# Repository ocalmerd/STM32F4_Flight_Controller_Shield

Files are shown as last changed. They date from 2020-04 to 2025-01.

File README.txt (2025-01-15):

Software is prepared as an Embedded C software, targetted to the STM32F407VGT6U MCU.
Hardware part is designed in Altium Designer and schematics & PCB design in ".Hardware" folder.

MERT OCAL

ocalmerd@gmail.com / mert.ocal@ogr.sakarya.edu.tr

https://www.linkedin.com/in/mert-ocal71/ / https://github.com/ocalmerd/

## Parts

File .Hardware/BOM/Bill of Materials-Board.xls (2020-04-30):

Item # | Designator | Description | Name | Quantity | Manufacturer 1 | Manufacturer Part Number 1 | Footprint | LibRef | Note
1 | C1, C2 | 220µF 16V Aluminum Electrolytic Capacitors Radial, Can - SMD 1000 Hrs @ 105°C | CAP ALUM 220UF 20% 16V SMD | 2 |  |  | CAP ALUM 6.6MM | 100uF 16V Aluminum(POL)
2 | D1 | Schottky Rectifier | SMAJ5.0A TVS Diyot | 1 |  |  | DO214AC SMA | SMAJ5.0A
3 | J1 | DC Power Jack Connector WR-DC, Male, Right Angled, THT, 5 A, 24 V | DC Power Jack | 1 |  |  | 694106301002 | 694106301002
4 | J2 | Header, 25-Pin, Dual row | Left Pins Connector | 1 |  |  | HDR2X25 | Header 25X2
5 | J3 | Header, 25-Pin, Dual row | Right Pins Connector | 1 |  |  | HDR2X25 | Header 25X2
6 | J4 | Header, 9-Pin | L3GD20H Connector | 1 |  |  | HDR1X9 | Header 9
7 | J5 | Header, 6-Pin, Right Angle | R9DS Receiver Connector | 1 |  |  | HDR1X6H | Header 6H
8 | J6 | Header, 4-Pin, Right Angle | 433MHz Air Connector | 1 |  |  | HDR1X4H | Header 4H
9 | J7 | Header, 3-Pin, Right Angle | ESC1 Connector | 1 |  |  | HDR1X3H | Header 3H
10 | J8 | Header, 3-Pin, Right Angle | ESC2 Connector | 1 |  |  | HDR1X3H | Header 3H
11 | J9 | Header, 3-Pin, Right Angle | ESC3 Connector | 1 |  |  | HDR1X3H | Header 3H
12 | J10 | Header, 3-Pin, Right Angle | ESC4 Connector | 1 |  |  | HDR1X3H | Header 3H
13 | U1 | Buck Switching Regulator IC Positive Fixed 5V 1 Output 3A TO-263-6, D²Pak (5 Leads + Tab), TO-263BA | LM2576HVS-5.0 REG BUCK 5V 3A TO263-5 | 1 |  |  | TO-263-6 | LM2576HVS-5.0--

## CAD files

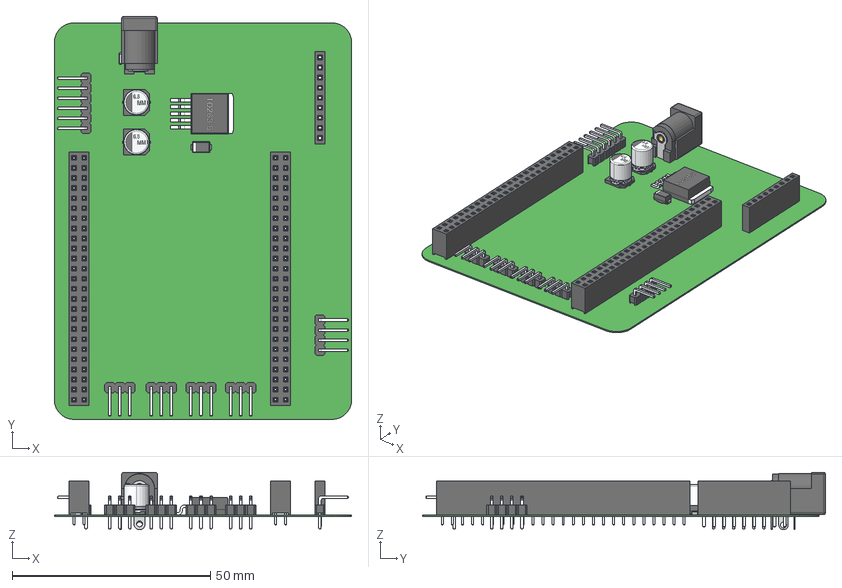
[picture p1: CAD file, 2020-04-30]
.Hardware/ExportSTEP/Board.step
75.0 x 101.6 x 14.5 mm
CAP_ALUM_6_6mm x 2
to263-5_p1-7_l10-2_w9-45
6941xx301002
694106301002_PinContact
6941xx301002_Back
6941xx301002_PinContact2
6941xx301002_PinLame
6941xx301002_PinBis
SMA

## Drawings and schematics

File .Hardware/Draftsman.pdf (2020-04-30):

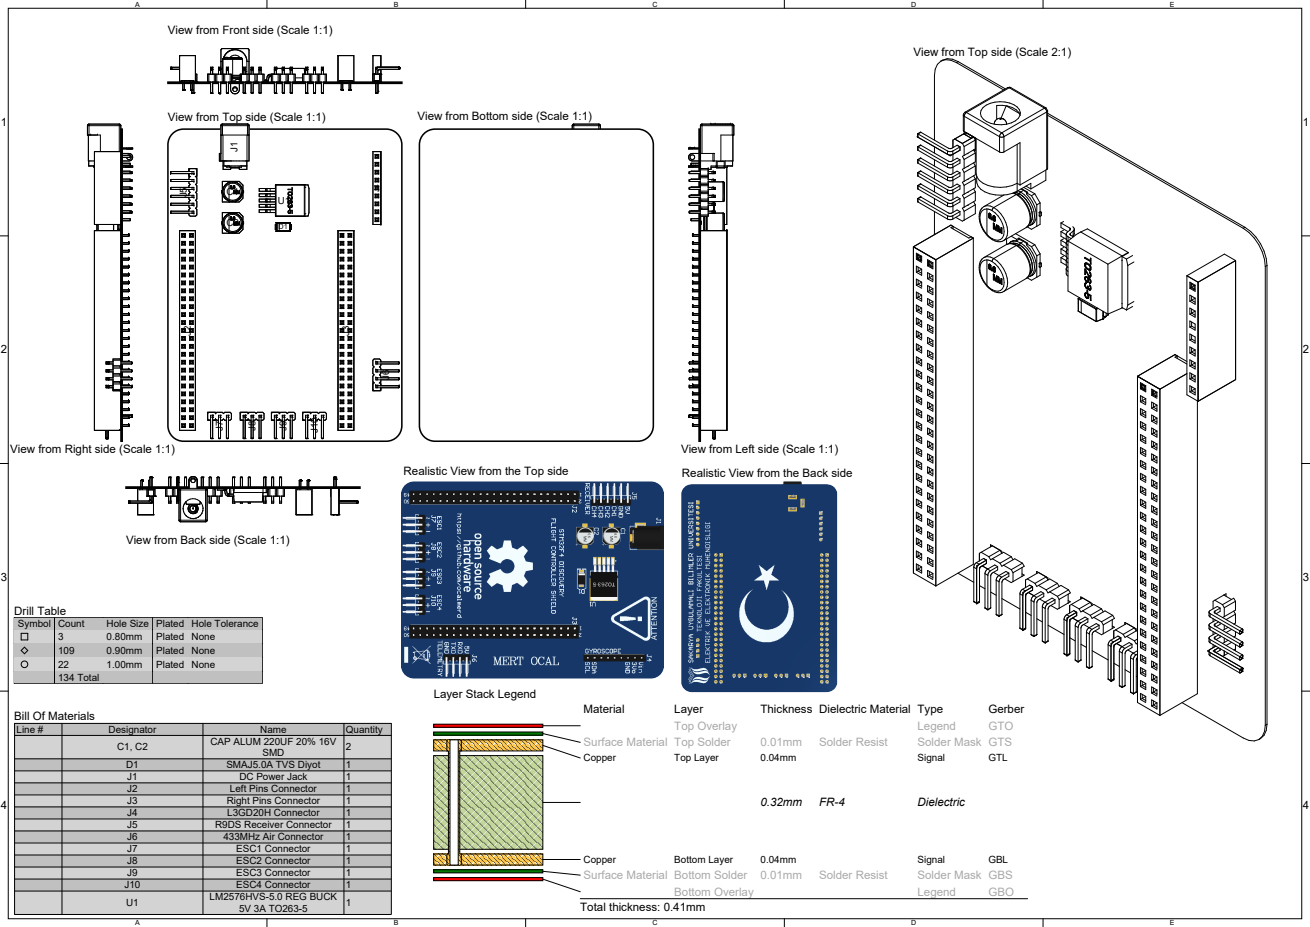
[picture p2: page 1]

View from Front side (Scale 1:1)

View from Top side (Scale 2:1)

View from Back side (Scale 1:1)

Symbol | Count | Hole Size | Plated | Hole Tolerance

3 | 0.80mm | Plated | None
109 | 0.90mm | Plated | None
22 | 1.00mm | Plated | None
134 Total

Line # | Designator | Name | Quantity

C1, C2 | CAP ALUM 220UF 20% 16V SMD | 2

D1 | SMAJ5.0A TVS Diyot | 1
J1 | DC Power Jack | 1
J2 | Left Pins Connector | 1
J3 | Right Pins Connector | 1
J4 | L3GD20H Connector | 1
J5 | R9DS Receiver Connector | 1
J6 | 433MHz Air Connector | 1
J7 | ESC1 Connector | 1
J8 | ESC2 Connector | 1
J9 | ESC3 Connector | 1
J10 | ESC4 Connector | 1
U1 | LM2576HVS-5.0 REG BUCK 5V 3A TO263-5 | 1

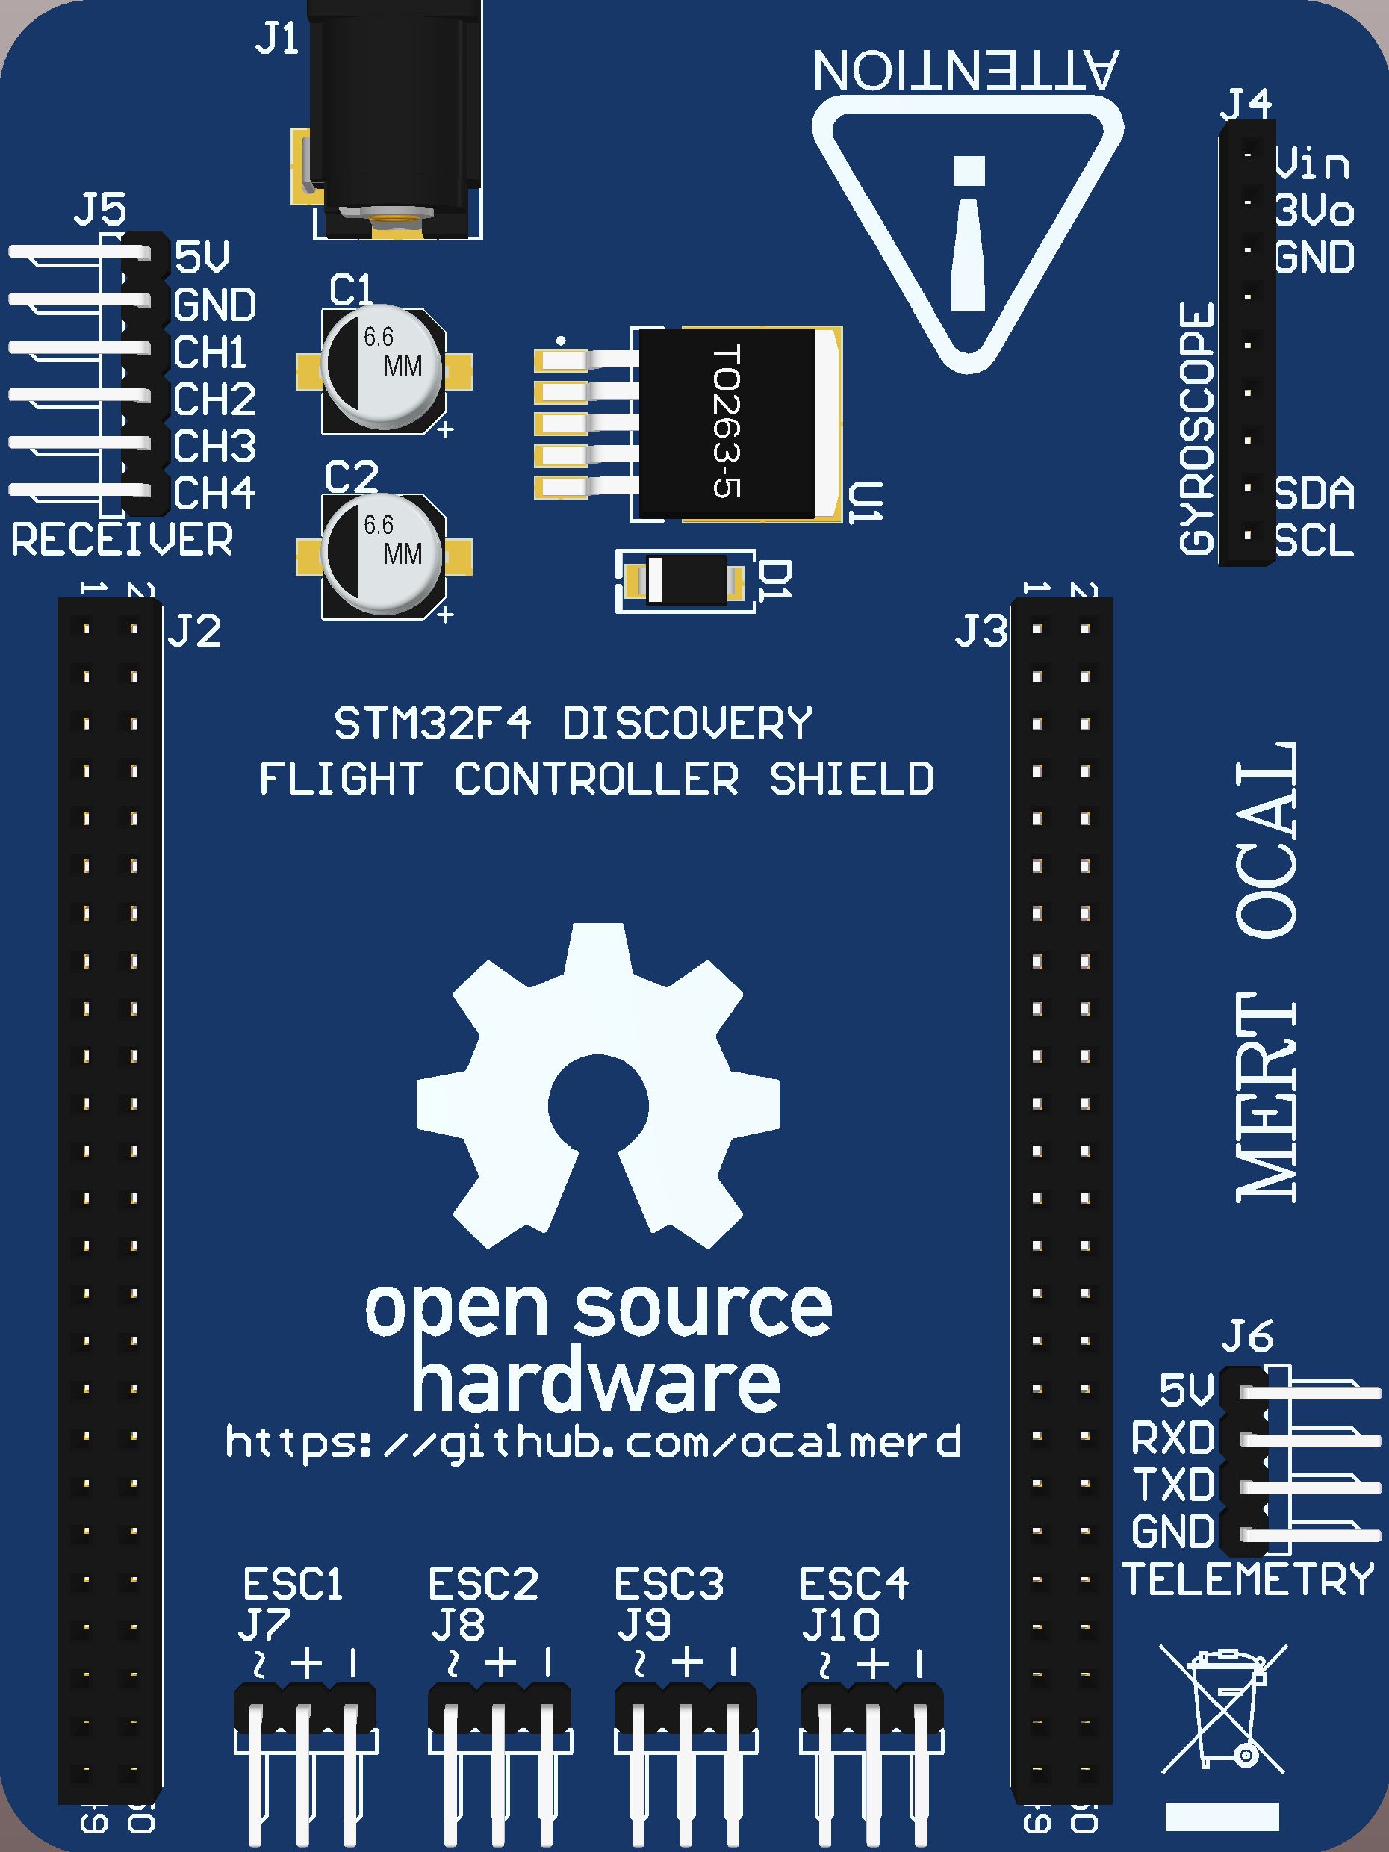
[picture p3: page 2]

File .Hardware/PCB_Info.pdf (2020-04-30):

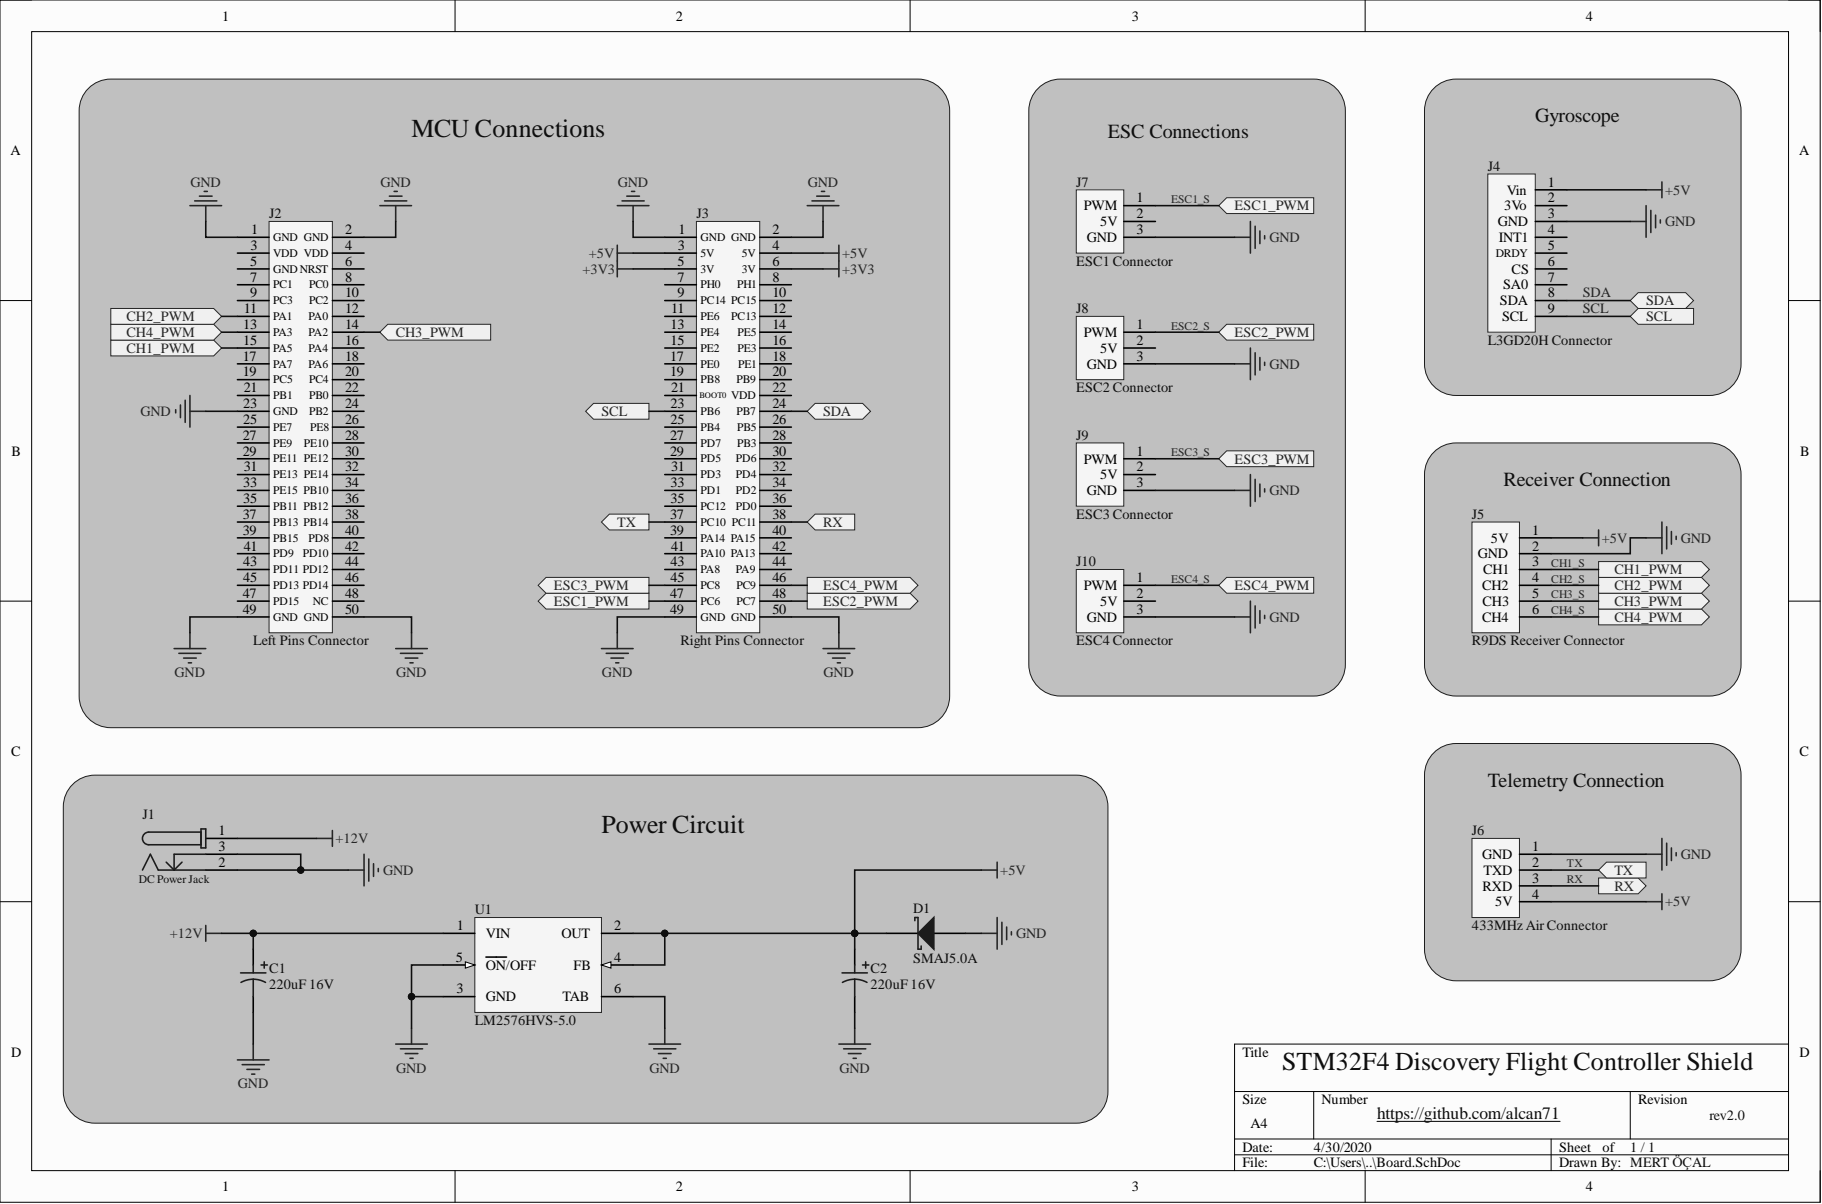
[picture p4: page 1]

Title
STM32F4 Discovery Flight Controller Shield

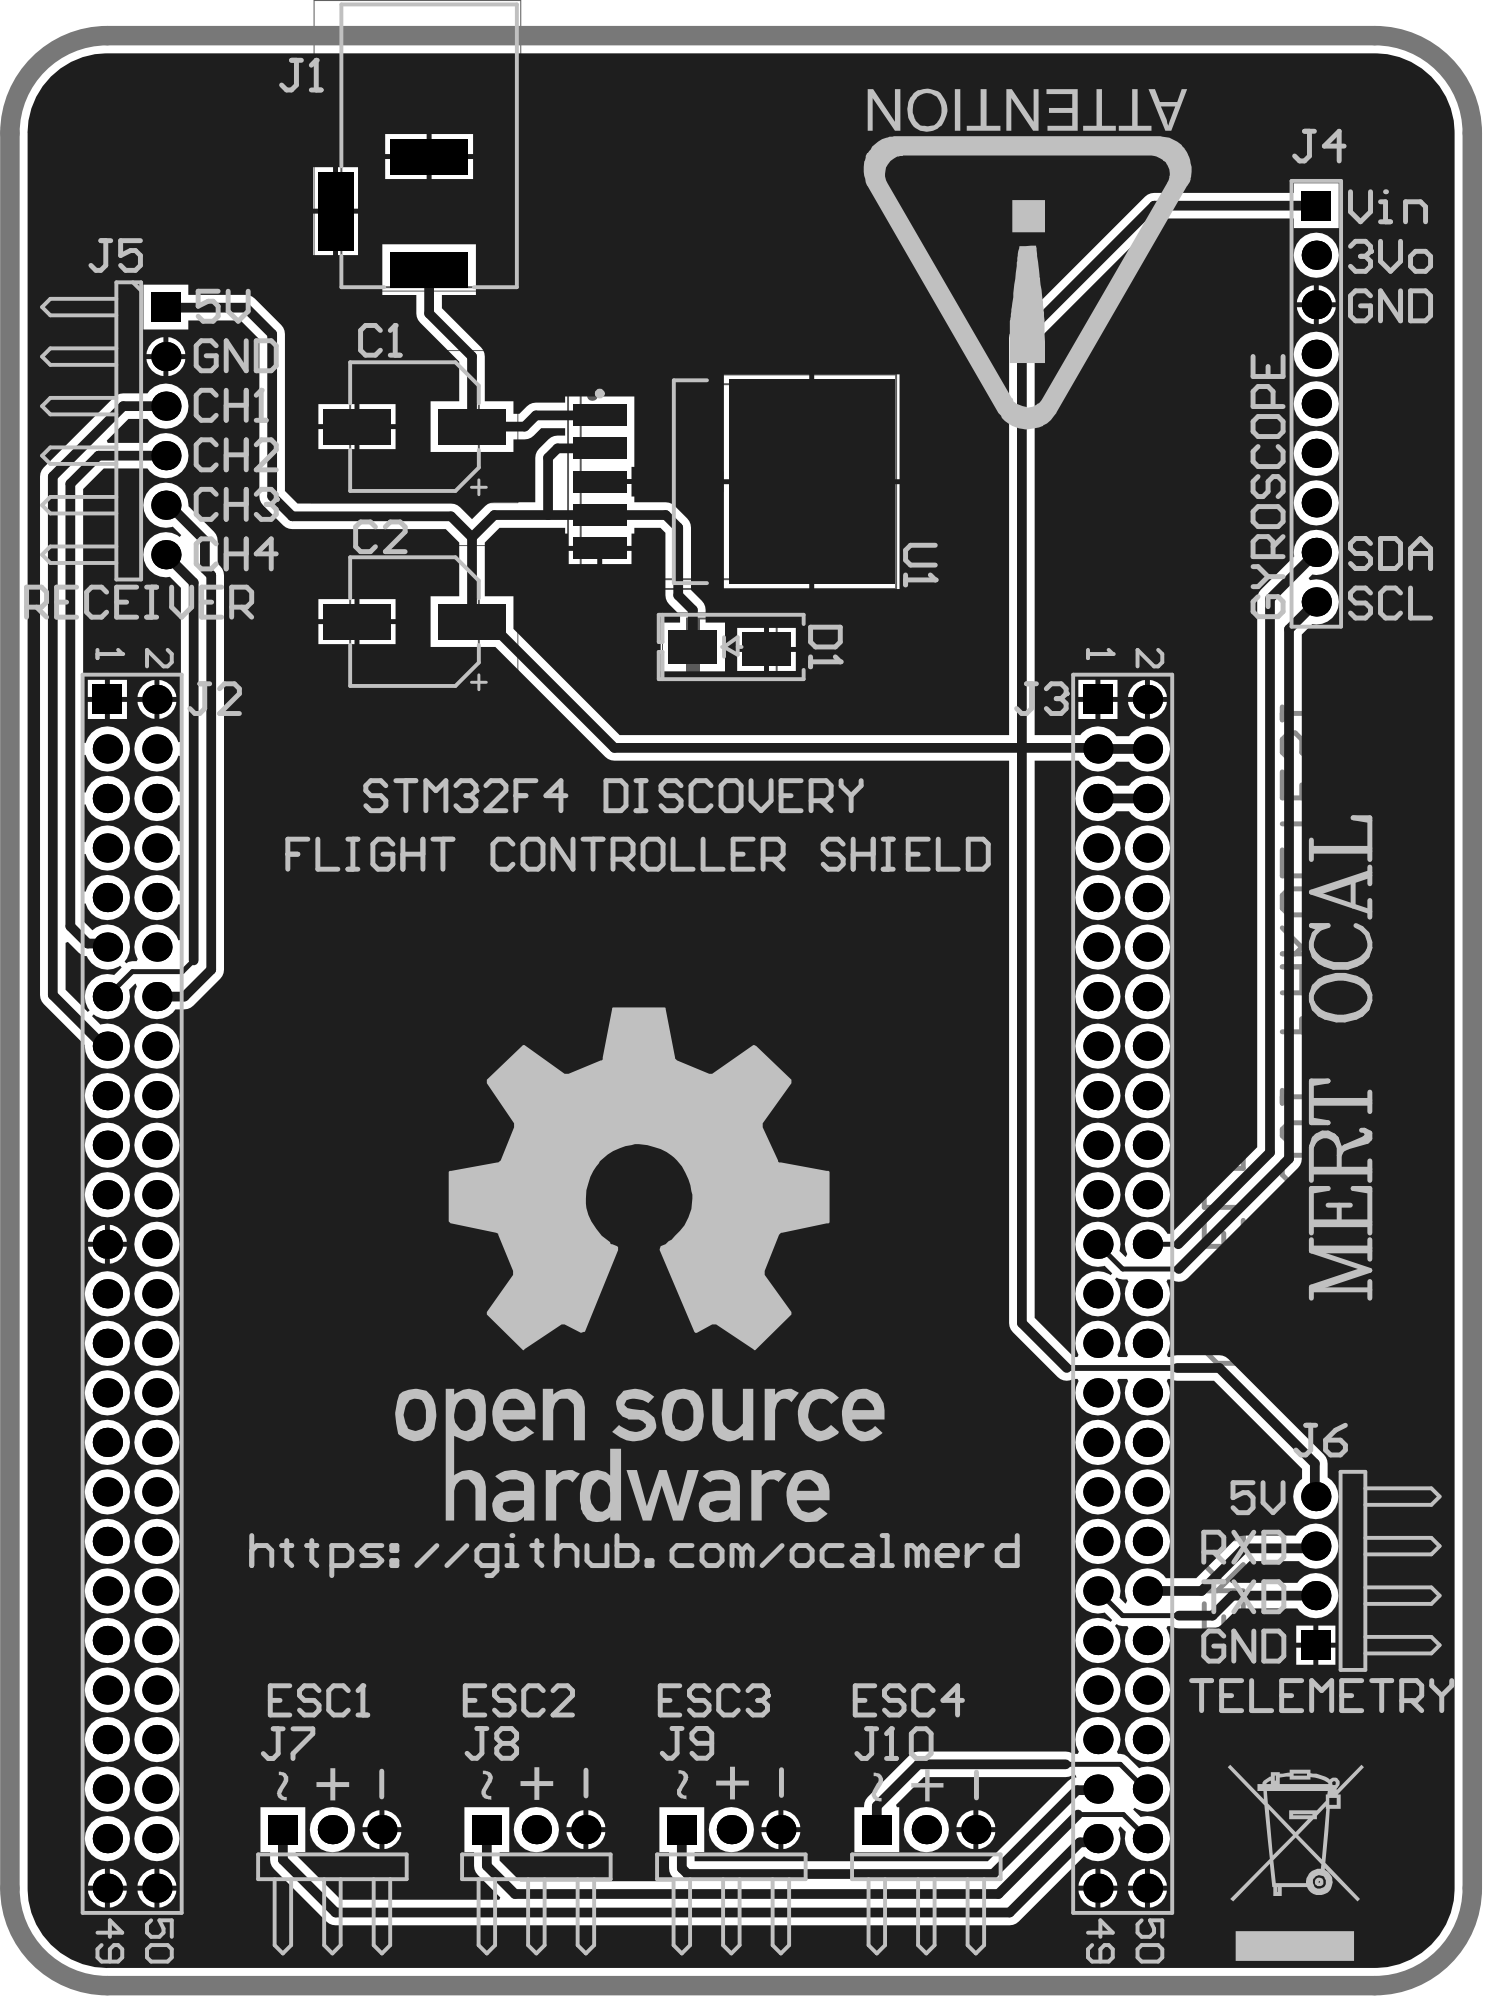
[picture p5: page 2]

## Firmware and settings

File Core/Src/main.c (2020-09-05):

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

/* Includes ------------------------------------------------------------------*/
#include "main.h"

/* USER CODE BEGIN Includes */
#include "PWM_IC.h"
#include "L3GD20H.h"
///
#include "Setup_FC.h"
#include "ESC_Calibration.h"
#include "Flight_Control.h"

/* USER CODE END Includes */

/* USER CODE BEGIN PTD */
char uartTX[101];
///	Inputs
int receiver_input_channel_1, receiver_input_channel_2, receiver_input_channel_3, receiver_input_channel_4;
int16_t gX_Raw, gY_Raw, gZ_Raw;
///
bool gyro_error = false;
///	Outputs
int esc_1, esc_2, esc_3, esc_4;
double gyro_pitch, gyro_roll, gyro_yaw;
///
uint8_t eeprom_data[32] = {0,0,0,0,0,0,0,0,0,0,0,0,0,0,0,0,0,0,0,0,0,0,0,0,0,0,0,0,0,0,0,0};
/* USER CODE END PTD */

I2C_HandleTypeDef hi2c1;

TIM_HandleTypeDef htim2;
TIM_HandleTypeDef htim3;

UART_HandleTypeDef huart4;

void SystemClock_Config(void);
static void MX_GPIO_Init(void);
static void MX_I2C1_Init(void);
static void MX_TIM2_Init(void);
static void MX_TIM3_Init(void);
static void MX_UART4_Init(void);
/**
  * @brief  The application entry point.
  * @retval int
  */
int main(void)
{
  /* MCU Configuration--------------------------------------------------------*/

  /* Reset of all peripherals, Initializes the Flash interface and the Systick. */
  HAL_Init();

  /* Configure the system clock */
  SystemClock_Config();

  /* USER CODE BEGIN SysInit */
  HAL_Delay( 2500 );
  /* USER CODE END SysInit */

  /* Initialize all configured peripherals */
  MX_GPIO_Init();
  MX_I2C1_Init();
  MX_TIM2_Init();
  MX_TIM3_Init();
  MX_UART4_Init();
  /* USER CODE BEGIN 2 */

	// Flash to EEPROM Array
	Flash_EEPROM_Data_Read( 11, 0x080E0000,  0, &eeprom_data[0]);
	Flash_EEPROM_Data_Read( 11, 0x080E0000,  1, &eeprom_data[1]);
	Flash_EEPROM_Data_Read( 11, 0x080E0000,  2, &eeprom_data[2]);
	Flash_EEPROM_Data_Read( 11, 0x080E0000,  3, &eeprom_data[3]);
	Flash_EEPROM_Data_Read( 11, 0x080E0000,  4, &eeprom_data[4]);
	Flash_EEPROM_Data_Read( 11, 0x080E0000,  5, &eeprom_data[5]);
	Flash_EEPROM_Data_Read( 11, 0x080E0000,  6, &eeprom_data[6]);
	Flash_EEPROM_Data_Read( 11, 0x080E0000,  7, &eeprom_data[7]);
	Flash_EEPROM_Data_Read( 11, 0x080E0000,  8, &eeprom_data[8]);
	Flash_EEPROM_Data_Read( 11, 0x080E0000,  9, &eeprom_data[9]);
	Flash_EEPROM_Data_Read( 11, 0x080E0000, 10, &eeprom_data[10]);
	Flash_EEPROM_Data_Read( 11, 0x080E0000, 11, &eeprom_data[11]);
	Flash_EEPROM_Data_Read( 11, 0x080E0000, 12, &eeprom_data[12]);
	Flash_EEPROM_Data_Read( 11, 0x080E0000, 13, &eeprom_data[13]);
	Flash_EEPROM_Data_Read( 11, 0x080E0000, 14, &eeprom_data[14]);
	Flash_EEPROM_Data_Read( 11, 0x080E0000, 15, &eeprom_data[15]);
	Flash_EEPROM_Data_Read( 11, 0x080E0000, 16, &eeprom_data[16]);
	Flash_EEPROM_Data_Read( 11, 0x080E0000, 17, &eeprom_data[17]);
	Flash_EEPROM_Data_Read( 11, 0x080E0000, 18, &eeprom_data[18]);
	Flash_EEPROM_Data_Read( 11, 0x080E0000, 19, &eeprom_data[19]);
	Flash_EEPROM_Data_Read( 11, 0x080E0000, 20, &eeprom_data[20]);
	Flash_EEPROM_Data_Read( 11, 0x080E0000, 21, &eeprom_data[21]);
	Flash_EEPROM_Data_Read( 11, 0x080E0000, 22, &eeprom_data[22]);
	Flash_EEPROM_Data_Read( 11, 0x080E0000, 23, &eeprom_data[23]);
	Flash_EEPROM_Data_Read( 11, 0x080E0000, 24, &eeprom_data[24]);
	Flash_EEPROM_Data_Read( 11, 0x080E0000, 25, &eeprom_data[25]);
	Flash_EEPROM_Data_Read( 11, 0x080E0000, 26, &eeprom_data[26]);
	Flash_EEPROM_Data_Read( 11, 0x080E0000, 27, &eeprom_data[27]);
	Flash_EEPROM_Data_Read( 11, 0x080E0000, 28, &eeprom_data[28]);
	Flash_EEPROM_Data_Read( 11, 0x080E0000, 29, &eeprom_data[29]);
	Flash_EEPROM_Data_Read( 11, 0x080E0000, 30, &eeprom_data[30]);
	Flash_EEPROM_Data_Read( 11, 0x080E0000, 31, &eeprom_data[31]);

	L3GD20H_Init();
	PWM_IC_Start();
	///
	HAL_Delay( 2500 );
	///

	if( gyro_error == true )
	{
		  sprintf(uartTX, "                                                                                                    ");
		  sprintf(uartTX, "\nSystem failed to start!\n");
		  HAL_UART_Transmit( &huart4, (uint8_t *)uartTX, sizeof(uartTX), 100 );

		  while ( gyro_error ) {	} 		// Endless Loop
	}

	sprintf(uartTX, "                                                                                                    ");
	sprintf(uartTX, "\nSystem started!\n");
	HAL_UART_Transmit( &huart4, (uint8_t *)uartTX, sizeof(uartTX), 100 );
	HAL_Delay( 2500 );

	if ( eeprom_data[31] == 92 )
	{

		  while ( HAL_GPIO_ReadPin(GPIOA, GPIO_PIN_0) )
		  {
			  for (int i = 0; i <= 50000000; i++ )
			  {
				  if( i == 50000000 && HAL_GPIO_ReadPin(GPIOA, GPIO_PIN_0) )
				  {
					  sprintf(uartTX, "                                                                                                    ");
					  sprintf(uartTX, "\nESC Calibration is starting! Reset after calibration!\n");
					  HAL_UART_Transmit( &huart4, (uint8_t *)uartTX, sizeof(uartTX), 100 );

					  ESC_Calibration();
				  }
			  }
		  }

		  /////////////////////////////////////////////////////////////////////////

		  sprintf(uartTX, "                                                                                                    ");
		  sprintf(uartTX, "\nFlight Control Setup is starting!\n");
		  HAL_UART_Transmit( &huart4, (uint8_t *)uartTX, sizeof(uartTX), 100 );

		  Flight_Control_Setup();

		  sprintf(uartTX, "                                                                                                    ");
		  sprintf(uartTX, "\nFlight Control Setup is done! Ready to fly!\n");
		  HAL_UART_Transmit( &huart4, (uint8_t *)uartTX, sizeof(uartTX), 100 );
	}
	else
	{
		  sprintf(uartTX, "                                                                                                    ");
		  sprintf(uartTX, "\nGubba nub nub doo rah kah!\n");
		  HAL_UART_Transmit( &huart4, (uint8_t *)uartTX, sizeof(uartTX), 100 );

		  Flash_EraseSector( 11 );
	}

	sprintf(uartTX, "                                                                                                    ");
	sprintf(uartTX, "\nWhat up, my glip-glops!!!\n");
	HAL_UART_Transmit( &huart4, (uint8_t *)uartTX, sizeof(uartTX), 100 );

  /* USER CODE END 2 */

  /* Infinite loop */
  /* USER CODE BEGIN WHILE */
  while (1)
  {
	  if ( HAL_GPIO_ReadPin(GPIOA, GPIO_PIN_0) )
	  {
		  for (int i = 0; i <= 50000000; i++ )
		  {
			  if( i == 50000000 && HAL_GPIO_ReadPin(GPIOA, GPIO_PIN_0) )
			  {
				  sprintf(uartTX, "                                                                                                    ");
				  sprintf(uartTX, "\nSetup is starting..!\n");
				  HAL_UART_Transmit( &huart4, (uint8_t *)uartTX, sizeof(uartTX), 100 );

				  Main_Setup( );
			  }
		  }
	  }

    /* USER CODE END WHILE */

    /* USER CODE BEGIN 3 */

	  Flight_Control_Loop();
  }
  /* USER CODE END 3 */
}

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


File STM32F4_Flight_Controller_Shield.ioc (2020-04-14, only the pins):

Mcu.UserName=STM32F407VGTx
PA0-WKUP.GPIO_Label=B1 [Blue PushButton]
PA0-WKUP.Signal=GPXTI0
PA1.Signal=S_TIM2_CH2
PA13.GPIO_Label=SWDIO
PA13.Signal=SYS_JTMS-SWDIO
PA14.GPIO_Label=SWCLK
PA14.Signal=SYS_JTCK-SWCLK
PA2.Signal=S_TIM2_CH3
PA3.Signal=S_TIM2_CH4
PA5.Signal=S_TIM2_CH1_ETR
PB2.GPIO_Label=BOOT1
PB2.Signal=GPIO_Input
PB6.Signal=I2C1_SCL
PB7.Signal=I2C1_SDA
PC0.GPIO_Label=OTG_FS_PowerSwitchOn
PC0.Signal=GPIO_Output
PC10.Signal=UART4_TX
PC11.Signal=UART4_RX
PC14-OSC32_IN.GPIO_Label=PC14-OSC32_IN
PC14-OSC32_IN.Signal=RCC_OSC32_IN
PC15-OSC32_OUT.GPIO_Label=PC15-OSC32_OUT
PC15-OSC32_OUT.Signal=RCC_OSC32_OUT
PC6.Signal=S_TIM3_CH1
PC7.Signal=S_TIM3_CH2
PC8.Signal=S_TIM3_CH3
PC9.Signal=S_TIM3_CH4
PD12.GPIO_Label=LD4 [Green Led]
PD12.Signal=GPIO_Output
PD13.GPIO_Label=LD3 [Orange Led]
PD13.Signal=GPIO_Output
PD14.GPIO_Label=LD5 [Red Led]
PD14.Signal=GPIO_Output
PD15.GPIO_Label=LD6 [Blue Led]
PD15.Signal=GPIO_Output
PH0-OSC_IN.GPIO_Label=PH0-OSC_IN
PH0-OSC_IN.Signal=RCC_OSC_IN
PH1-OSC_OUT.GPIO_Label=PH1-OSC_OUT
PH1-OSC_OUT.Signal=RCC_OSC_OUT

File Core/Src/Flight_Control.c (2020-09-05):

/*
 * Flight_Control.c
 *
 *  Created on: 19 mar. 2020
 *      Author: MERT OCAL
 */

#include "Flight_Control.h"


///////////////////////////////////////////////////////////////////////////////////////////////////////////////////////////////////////
//PID gain and limit settings
///////////////////////////////////////////////////////////////////////////////////////////////////////////////////////////////////////
float pid_p_gain_roll = 2.4;               	//Gain setting for the roll P-controller 		- (1.6)
float pid_i_gain_roll = 0.008;              //Gain setting for the roll I-controller 		- (0.007)
float pid_d_gain_roll = 120;                //Gain setting for the roll D-controller 		- (100)
int pid_max_roll = 400;                   	//Maximum output of the PID-controller (+/-) 	- (400)

float pid_p_gain_pitch = 2.4;    			//Gain setting for the pitch P-controller		- (1.6)
float pid_i_gain_pitch = 0.008;  			//Gain setting for the pitch I-controller 		- (0.007)
float pid_d_gain_pitch = 120;  				//Gain setting for the pitch D-controller 		- (100)
int pid_max_pitch = 400;          			//Maximum output of the PID-controller (+/-)    - (400)

float pid_p_gain_yaw = 4.0;                	//Gain setting for the pitch P-controller 		- (4.0)
float pid_i_gain_yaw = 0.02;               	//Gain setting for the pitch I-controller  		- (0.02)
float pid_d_gain_yaw = 0.0;                	//Gain setting for the pitch D-controller   	- (0)
int pid_max_yaw = 400;                     	//Maximum output of the PID-controller (+/-) 	- (400)

float pid_error_temp;
float pid_i_mem_roll, pid_roll_setpoint, gyro_roll_input, pid_output_roll, pid_last_roll_d_error;
float pid_i_mem_pitch, pid_pitch_setpoint, gyro_pitch_input, pid_output_pitch, pid_last_pitch_d_error;
float pid_i_mem_yaw, pid_yaw_setpoint, gyro_yaw_input, pid_output_yaw, pid_last_yaw_d_error;

///////////////////////////////////////////////////////////////////////////////////////////////////////////////////////////////////////
//Declaring global variables
///////////////////////////////////////////////////////////////////////////////////////////////////////////////////////////////////////
int start, throttle, cal_int = 0;
int receiver_input[5];
double gyro_axis[4], gyro_axis_cal[4];
//
extern int esc_1, esc_2, esc_3, esc_4;
extern int receiver_input_channel_1, receiver_input_channel_2, receiver_input_channel_3, receiver_input_channel_4;
//
extern int16_t gX_Raw, gY_Raw, gZ_Raw;
extern double gyro_pitch, gyro_roll, gyro_yaw;
//
extern uint8_t eeprom_data[32];


void Flight_Control_Setup( void )
{
	HAL_Delay( 3000 );

	//Let's take multiple gyro data samples so we can determine the average gyro offset (calibration).
	for ( cal_int = 0; cal_int < 2000 ; cal_int ++ )				//Take 2000 readings for calibration.
	{
		Flight_Gyro_Signalen();                                           //Read the gyro output.

		gyro_axis_cal[1] += gyro_axis[1];                          //Ad roll value to gyro_roll_cal.
		gyro_axis_cal[2] += gyro_axis[2];                          //Ad pitch value to gyro_pitch_cal.
		gyro_axis_cal[3] += gyro_axis[3];                          //Ad yaw value to gyro_yaw_cal.                                               //Wait 3 milliseconds before the next loop.
	}

	//Now that we have 2000 measures, we need to divide by 2000 to get the average gyro offset.
	gyro_axis_cal[1] /= 2000;                                    //Divide the roll total by 2000.
	gyro_axis_cal[2] /= 2000;                                    //Divide the pitch total by 2000.
	gyro_axis_cal[3] /= 2000;                                    //Divide the yaw total by 2000.

	//Wait until the receiver is active and the throttle is set to the lower position.
	while( receiver_input_channel_3 > 1100 )
	{
		receiver_input_channel_3 = Convert_Receiver_Channels(3);    //Convert the actual receiver signals for throttle to the standard 1000 - 2000us
		receiver_input_channel_4 = Convert_Receiver_Channels(4);    //Convert the actual receiver signals for yaw to the standard 1000 - 2000us
	}

	PWM_Output_Start();
	PWM_Output_Idle();

	start = 0;           //Set start back to 0.
}

void Flight_Control_Loop( void )
{
	receiver_input_channel_1 = Convert_Receiver_Channels(1);      // Convert the actual receiver signals for pitch to the standard 1000 - 2000us.
	receiver_input_channel_2 = Convert_Receiver_Channels(2);      // Convert the actual receiver signals for roll to the standard 1000 - 2000us.
	receiver_input_channel_3 = Convert_Receiver_Channels(3);      // Convert the actual receiver signals for throttle to the standard 1000 - 2000us.
	receiver_input_channel_4 = Convert_Receiver_Channels(4);      // Convert the actual receiver signals for yaw to the standard 1000 - 2000us.

	//Let's get the current gyroscope data and scale it to degrees per second for the PID calculations.
	Flight_Gyro_Signalen();

	gyro_roll_input 	= ( gyro_roll_input * 0.8 )	+ ( ( gyro_roll 	/ 57.14286 ) * 0.2);      // Gyroscope PID input is deg/sec.
	gyro_pitch_input 	= ( gyro_pitch_input * 0.8) + ( ( gyro_pitch    / 57.14286 ) * 0.2);      // Gyroscope PID input is deg/sec.
	gyro_yaw_input		= ( gyro_yaw_input * 0.8  ) + ( ( gyro_yaw 	    / 57.14286 ) * 0.2);      // Gyroscope PID input is deg/sec.

	//For starting the motors: throttle low and yaw left (step 1).
	if( receiver_input_channel_3 < 1100 && receiver_input_channel_4 < 1100 )
	{
//		if ( L3GD20H_Connection_Check() )
//		{
		start = 1;
//		}
	}

	//When yaw stick is back in the center position start the motors (step 2).
	if( start == 1 && receiver_input_channel_3 < 1100 && receiver_input_channel_4 > 1400 )
	{
		start = 2;

		//Reset the PID controllers for a bumpless start.
		pid_i_mem_roll = 0;
		pid_last_roll_d_error = 0;
		pid_i_mem_pitch = 0;
		pid_last_pitch_d_error = 0;
		pid_i_mem_yaw = 0;
		pid_last_yaw_d_error = 0;
	}

	//Stopping the motors: throttle low and yaw right.
	if( start == 2 && receiver_input_channel_3 < 1100 && receiver_input_channel_4 > 1900 )
	{
		start = 0;

		PWM_Output_Idle();
	}

	//The PID set point in degrees per second is determined by the roll receiver input.
	//In the case of dividing by 3 the max roll rate is approximately 164 degrees per second ( (500-8)/3 = 164d/s ).
	pid_roll_setpoint = 0;
	//We need a little dead band of 16us for better results.
	if     ( receiver_input_channel_1 > 1508 )	{	pid_roll_setpoint = (receiver_input_channel_1 - 1508)/3.0;	}
	else if( receiver_input_channel_1 < 1492 )	{	pid_roll_setpoint = (receiver_input_channel_1 - 1492)/3.0;	}
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

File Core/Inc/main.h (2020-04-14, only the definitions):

#define PC14_OSC32_IN_Pin GPIO_PIN_14
#define PC14_OSC32_IN_GPIO_Port GPIOC
#define PC15_OSC32_OUT_Pin GPIO_PIN_15
#define PC15_OSC32_OUT_GPIO_Port GPIOC
#define PH0_OSC_IN_Pin GPIO_PIN_0
#define PH0_OSC_IN_GPIO_Port GPIOH
#define PH1_OSC_OUT_Pin GPIO_PIN_1
#define PH1_OSC_OUT_GPIO_Port GPIOH
#define OTG_FS_PowerSwitchOn_Pin GPIO_PIN_0
#define OTG_FS_PowerSwitchOn_GPIO_Port GPIOC
#define B1_Pin GPIO_PIN_0
#define B1_GPIO_Port GPIOA
#define BOOT1_Pin GPIO_PIN_2
#define BOOT1_GPIO_Port GPIOB
#define LD4_Pin GPIO_PIN_12
#define LD4_GPIO_Port GPIOD
#define LD3_Pin GPIO_PIN_13
#define LD3_GPIO_Port GPIOD
#define LD5_Pin GPIO_PIN_14
#define LD5_GPIO_Port GPIOD
#define LD6_Pin GPIO_PIN_15
#define LD6_GPIO_Port GPIOD
#define SWDIO_Pin GPIO_PIN_13
#define SWDIO_GPIO_Port GPIOA
#define SWCLK_Pin GPIO_PIN_14
#define SWCLK_GPIO_Port GPIOA

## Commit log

2020-04-17 Gryo_error loop fix
    Added while loop in case of gyro error.
    [main.c]
2020-04-17 PID update
    PID parameters update
2020-04-28 PID Update
    Kp updated
2020-04-30 Hardware & PID
    Hardware part of the project is added & PID Update
    [Bill of Materials-Board.xls, Bill of Materials-Board.xlsx, Board.step]
2020-05-07 PID & Gyro CC
    PID paramteres updated & Gyro connection check function added

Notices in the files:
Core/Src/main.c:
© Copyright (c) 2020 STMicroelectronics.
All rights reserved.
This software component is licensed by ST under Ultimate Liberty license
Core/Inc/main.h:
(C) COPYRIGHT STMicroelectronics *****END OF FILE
